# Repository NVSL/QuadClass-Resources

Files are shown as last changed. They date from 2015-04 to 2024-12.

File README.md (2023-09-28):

# The Quadcopter Class

Welcome to CSE176e Robotic System Design and Implementation (AKA, the Quadcopter Class).

This repo serves an the homepage for the course labs. It contains all
the lab write ups and several resources you will use throughout the
course.

- `labs` has all the labs. The write ups reference the starter repos they use.
- `Fusion 360` has the pre-built parts library, CAM files, and design rule files to use with Fusion 360.
- `Lecture Slides` has slides that aren't part of any particular lab.

Please see the [course home page](https://sites.google.com/ucsd.edu/the-quadcopter-class/home) or the [class calendar](ohttps://docs.google.com/spreadsheets/d/1cgSJm-5A6JrrA-iNKX8d2A0SE1PBk1CwzLvdhLKHuWY/) for schedule, due dates, and other logistical issues.

## A Note About Software Tool Names

The PCB design software we use is called Fusion 360. It used to be known as "Eagle". I've mostly updated the course materials to reflect this change.  If you see "Eagle" you should think "Fusion 360".

## Overview

We are going to build remote-controlled quadcopters from scratch in 10 weeks.

The goals for the course are for you to learn how to design, assemble, and program a moderately complex electronic device. The device you will build is a small, remote-controlled quadcopter similar to this:

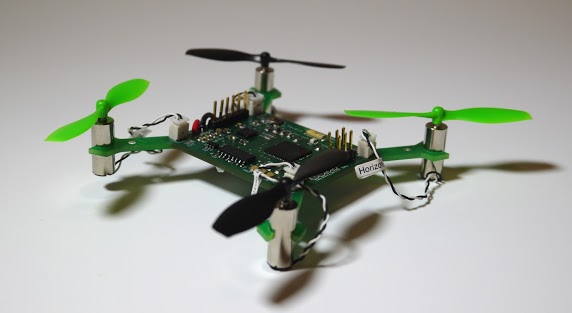
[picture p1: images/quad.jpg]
Example Quadcopter


In particular, you'll learn and/or practice these skills/topics:

- Printed circuit board design
  - Implementing a spec
  - Leveraging reference designs
  - Interpreting data sheets
  - Selecting parts
- PCB Assembly
  - Concepts
  - Moderately advanced soldering
- Embedded Systems Programming
  - Real-time
  - Resource constrained
- Basic Sensor fusion
- Basic Control Theory

## Labs

There are 10 labs divided into four sections. Deadlines are on the course homepage.

The slides for each lab are in the directory with the lab description.

### PCB Design

1. [Introduction To Fusion 360](https://github.com/NVSL/QuadClass-Resources/tree/master/labs/Introduction-To-Eagle)
2. [Building Parts In Fusion 360](https://github.com/NVSL/QuadClass-Resources/tree/master/labs/Building-Parts-In-Eagle)
3. [Building The Quadcopter Schematic](https://github.com/NVSL/QuadClass-Resources/tree/master/labs/Building-The-Quadcopter-Schematic)
4. [Laying Out The Board](https://github.com/NVSL/QuadClass-Resources/tree/master/labs/Laying-Out-The-Board)
5. [Manufacturing The Board](https://github.com/NVSL/QuadClass-Resources/tree/master/labs/Manufacturing-The-Board)

### PCB Assembly

6. [Assembling A PCB](https://github.com/NVSL/QuadClass-Resources/tree/master/labs/Assembling-A-PCB)

### Software

7. [Programming The Hardware](https://github.com/NVSL/QuadClass-Resources/tree/master/labs/Programming-The-Hardware)
8. [Sensing and Control](https://github.com/NVSL/QuadClass-Resources/tree/master/labs/Sensing-And-Control)
<!-- 8. [Sensing and Filtering](https://github.com/NVSL/QuadClass-Resources/tree/master/labs/Sensing-And-Filtering)-->
<!-- 9. [Implementing PID](https://github.com/NVSL/QuadClass-Resources/tree/master/labs/Implementing-PID)-->

### Flight

9. [Flight](https://github.com/NVSL/QuadClass-Resources/tree/master/labs/Flight)
10. [Cleanup](https://github.com/NVSL/QuadClass-Resources/tree/master/labs/Cleanup)

## Lab Equipment

The course requires several pieces of equipment:

1. A remote control.
2. A PID test stand.
3. A quadcopter prototype.
4. Miscelleneous cables, parts, etc.

You will also build a quadcopter, which you can also keep.

### Keeping the Remote

You cannot keep the remote you used in class. However, I a limited number of older remote boards that you can have if you really want one. Please talk to me near the end of the course, if you are interested.

### Returning the Equipment

The PID test stand, flight control board, remote, and other miscelleneous equipment you borrow for the labs must be returned or replaced (modulo normal wear and tear) before I will assign you a grade in the course.

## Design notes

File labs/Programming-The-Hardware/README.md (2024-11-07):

# Arduino, Wireless, and Quadcopter Hardware

This is big lab, but there shouldn’t be many surprises. You’re mostly getting parts and pieces together for future labs, but you do have to integrate everything into one app at the end, and integration is always harder than you think.  
There’s a lot to do. Get started!

## Pick your Team

You will work on this lab and all future labs in teams of two. You will need to create a team on Eaglint and via the github classroom interface. The name of your team in github classroom must match the team name you use in Eaglint, or Eaglint will refuse to check your work.

## Skills to Learn

1. Installing the Arduino GUI.
2. Programming your remote and the flight control board.
3. Communicating with the boards using an FTDI serial port.
4. Communicate wirelessly between the remote and the FCB.
5. Reading values from the controller gimbals.
6. Use the other features of the remote.
7. Driving a DC motor with PWM.

## Equipment, Supplies, and Software You Will Need

1. Create a team in eaglint. You _must_ do this before clicking the starter link below.
2. The starter repo for this lab: https://classroom.github.com/a/a_OCsamt.
4. Test stand and remote control part kit.
5. Laser-cut parts for a test stand and airframe.
6. 1 micro USB cable.
7. 1 flight control board (FCB).
8. Three LiPo batteries.
9. 1 set of motors.
10. 1 set of matched propellers (2xCW, 2xCCW)

### Your Remote Control

You are responsible for the care of the remote:

1. If you break it, you'll need to pay replace the broken parts.
2. Be reasonably gentle with the gimbals (joysticks). They are of high quality, but are not indestructible.

Unfortunately, you cannot keep the remote. However, it is pretty easy to build you own. Ask the professor, if you are interested.

### Your Flight Control Board and Test Stand

The flight control board (FCB) is a PCB very similar to the quadcopter
you will eventually build. It mounts to the test stand and will
provide a platform for your initial quadcopter firmware development.
The FCBs are provided for your use during the class.

## Preliminaries

### Install Arduino

Install Arduino 2.3.3. This is the only version we will be supporting in class.  
[Arduino Download](https://www.arduino.cc/en/software)

### Setup Your Firmware Development Environment

The repo you create and use for this lab will be the repository you use for your software development during the rest of the class. The `firmware` directory is organized as an Arduino Sketchbook, which means the Arduino toolchain and IDE know where to look for things. To use it, you’ll need to set that directory as your sketch book directory in Arduino.  
(`File->Preferences->Sketchbook location`).  
Then, enter your github repo firmware folder path, example: `../<github_repo>/firmware`

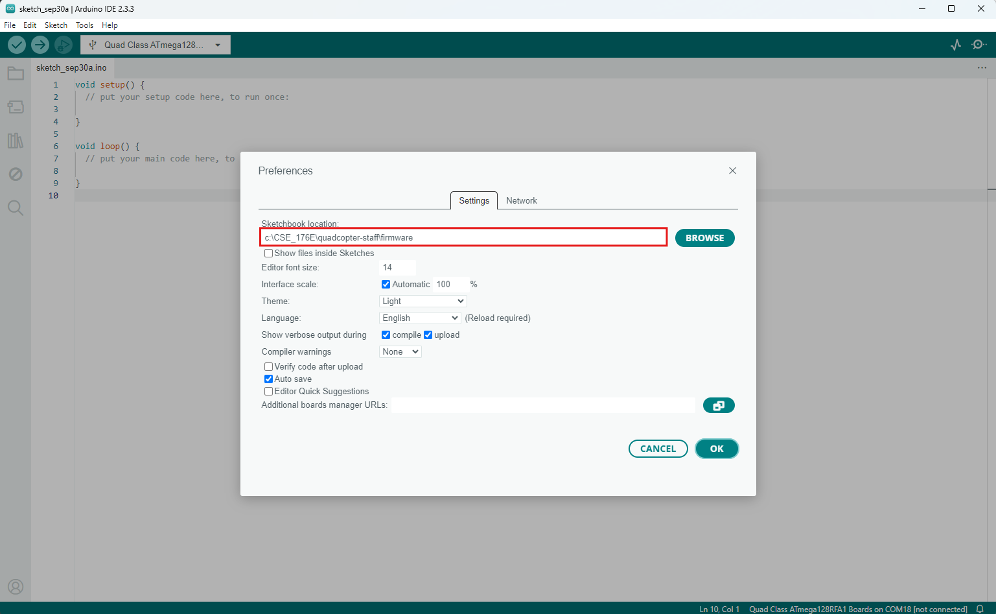
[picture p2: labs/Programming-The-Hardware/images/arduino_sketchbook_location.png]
Sketchbook Path


#### Add Board Definition Files

This will let Arduino talk to all the [Atmega128RFA](https://www.digikey.com/en/products/detail/microchip-technology/ATMEGA128RFA1-ZU/2208800) boards we will be using in this class, including your quadcopter.

- Clone the Arduino addon (https://github.com/NVSL/QuadClass_Atmega128RFA_Arduino_Addon) into `firmware/hardware`. You should end up with this directory `firmware/hardware/QuadClass_Atmega128RFA_Arduino_Addon/avr`.
- Restart Arduino. Then, under `Tool->Board` you should see `Quad Class ATmega128RFA1 Boards`. Select that board.
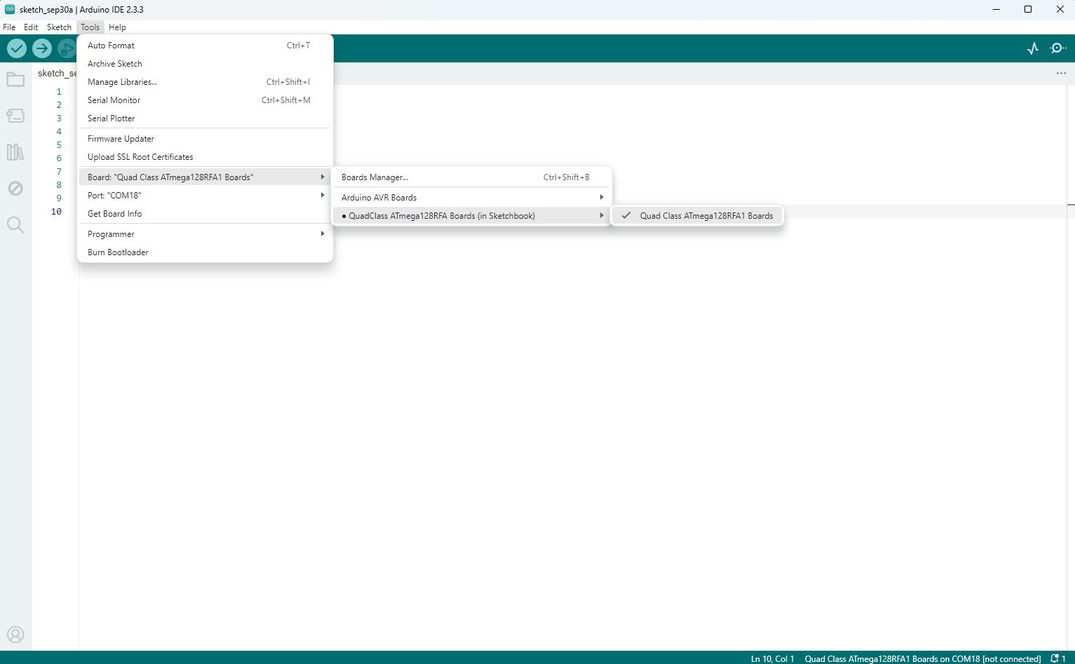
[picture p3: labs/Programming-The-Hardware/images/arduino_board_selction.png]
Board Selection
  
- Select `Tools->Programmer->USBTinyISP`

#### Install the Libraries

You’ll need a few libraries, so you might as well install them now, but you won’t use all of them in this lab:

Clone them into `firmware/libraries`.

1. Attitude, Heading, and Reference System (AHRS): https://github.com/NVSL/QuadClass_AHRS.git
2. LSM6DSOX library: https://github.com/NVSL/QuadClass-LSM6DSOX.git
3. Adafruit unified sensor library: https://github.com/NVSL/QuadClass_Sensor.git
4. Sparkfun SerLCD library: https://github.com/sparkfun/SparkFun_SerLCD_Arduino_Library.git

Here's the command sequence on my machine:

```
(cd ./firmware/libraries/; git clone git@github.com:NVSL/QuadClass-AHRS.git)
(cd ./firmware/libraries/; git clone git@github.com:NVSL/QuadClass-LSM6DSOX.git)
(cd ./firmware/libraries/; git clone git@github.com:NVSL/QuadClass-Sensor.git)
(cd ./firmware/libraries/; git clone git@github.com:sparkfun/SparkFun_SerLCD_Arduino_Library.git)
(cd ./firmware/hardware/;  git clone git@github.com:NVSL/QuadClass-Atmega128RFA-Arduino-Addon.git)
```

Go to Library Manager and install "Adafruit LSM6DS". A pop-up window will show up, click "Install ALL".  
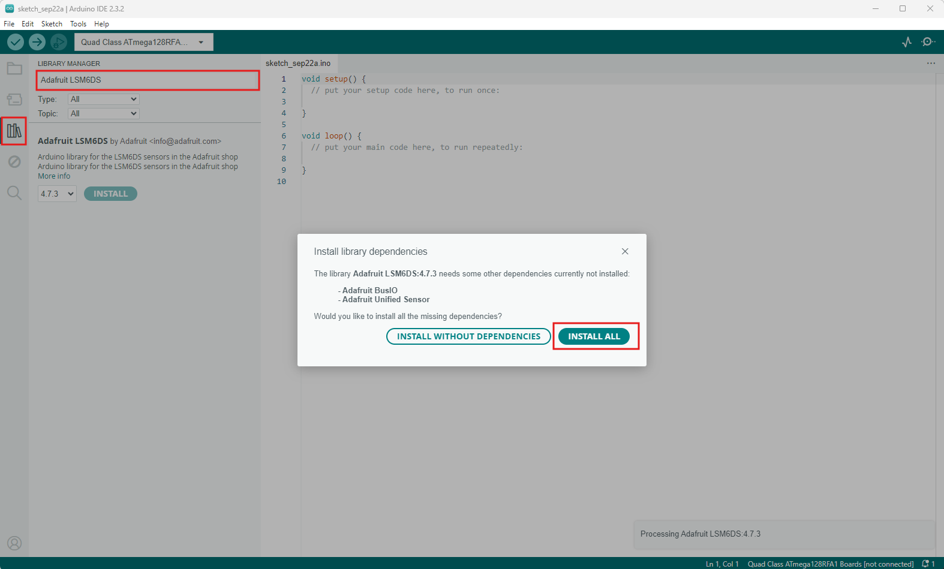
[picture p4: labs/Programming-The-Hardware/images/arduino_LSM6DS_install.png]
Install Adafruit LSM6DS


When you're done, the top few levels of your repo should look like this:

```
./firmware
./firmware/hardware
./firmware/hardware/QuadClass-Atmega128RFA-Arduino-Addon
./firmware/RFEcho
./firmware/RFEcho/RFEcho.ino
./firmware/RFChat
./firmware/RFChat/RFChat.ino
./firmware/libraries
./firmware/libraries/Radio
./firmware/libraries/SparkFun_SerLCD_Arduino_Library
./firmware/libraries/RotaryEncoder
./firmware/libraries/QuadClass-Sensor
./firmware/libraries/QuadClass-AHRS
./firmware/libraries/QuadClass-LSM6DSOX
./firmware/libraries/Adafruit_BusIO
./firmware/libraries/Adafruit_LSM6DS
./firmware/libraries/Adafruit_Unified_Sensor
./firmware/libraries/Remote
./firmware/libraries/SoftwareSerial2
./firmware/RFCount
./firmware/RFCount/RFCount.ino
./hardware
```

Restart Arduino and the bottom of your `Sketch->Include Library` menu should look something like this:

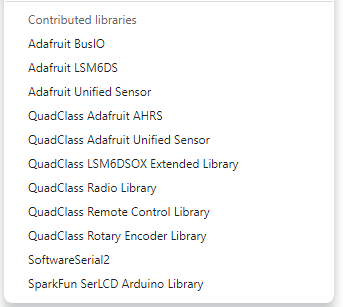
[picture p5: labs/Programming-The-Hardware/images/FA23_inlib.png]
Libraries installed


#### Getting Updates For the Starter Repo

Occasionally, I find bugs in the starter repo and push updates to it. To get them you need to 'fetch from upstream' using git. The first time you do this you need to do:

`git remote add upstream git@github.com:UCSD-Quadcopter-Class/QuadClass-Quadcopter-Starter-sp23.git`

Then, each time I push a new update you should do this:

```
git fetch upstream
git merge remotes/upstream/master
git push
```

I'll announce pushes on Piazza.

#### Create Your Firmware Source Files

Create sketches for your quad and remote control firmware.

- `firmware/quad_firmware/quad_firmware.ino` will hold the firmware (i.e., flight control software) for your quadcopter
- `firmware/remote_firmware/remote_firmware.ino` will hold the code for your remote control.

Add the following code to `remote_firmware.ino`:

```
#include <radio.h>
#include "quad_remote.h"      // Header file with pin definitions and setup
#include <serLCD.h>
serLCD lcd;

void setup() {
}

void loop() {
}
```

### Arduino Troubleshooting

Programming Arduino microcontrollers (i.e., transfering the compiled to the device) can be a temperamental process. If you get an error while programming the board, there are many different things you can try to make it work (some of which seem like magic):

- Make sure you have the right board and programmer selected.
  - On a Mac, this will be something like `/dev/cu.usbserial-AG0JL8H4`. It is definitely not anything like `tty.usbserial-AG0JL8H4` or `cu.Bluetooth-Incoming-Port` or `cu.iPhone-WirelessiAPv2`.
  - On a PC, it is probably the highest-numbered "COM" port.
- Try a different USB port. Laptops generally have multiple, internal USB hubs and some don’t play well with Arduino.
- Try a USB 2.0 port. Sometimes programming doesn’t work over USB 3.0. If your computer has a USB 2.0 hub use it. If not, get a USB 2.0 hub and plug the Arduino into that. On some machines the blue USB ports are 3.0 and black ones are 2.0.
- Unplug everything, quit Arduino, plug everything back in, restart Arduino.
- Google the error. Chances are you are not alone.

In rare cases, you may need to install drivers for the FTDI programming board. Read the How to Install FTDI Drivers Tutorial https://learn.sparkfun.com/tutorials/how-to-install-ftdi-drivers.

## Bringing Up the Remote

Your first task to "bring up" your remote. This means verifying that all of it's components work and that you can successfully access them via software.

**Note:** You don't need to assemble it anymore, we will provide an assembled remotes.
### Assembling the Remote

Many of you will receive a partially assembled remote. Follow along in here to add the parts that are missing.

**The pictures below are for an older model of the remote. The steps are very similar. Differences are noted.**

To assemble the remote you will need the following **FIXME CHECK**:

- 8x 1-inch standoffs
- 4x 1/2-inch standoffs
- 4x 3/8-inch standoffs
- 8x 1-1/2-inch screws
- 4x 1-1/4-inch screws
- 12x nuts
- 4x small zip ties
- 1x PCB
- 1x LCD
- 1x battery cable
- 2x gimbals
- 1x USB Micro cable

##### Steps

**All the Parts**

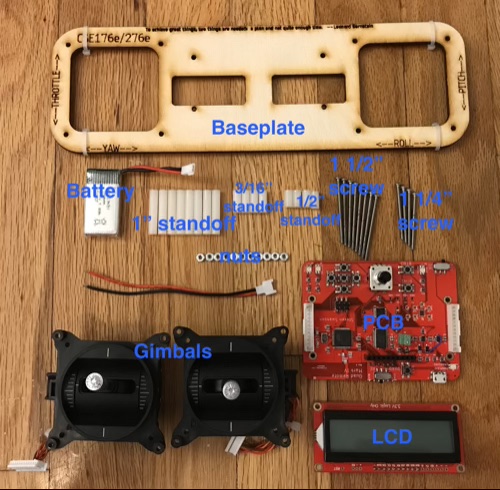
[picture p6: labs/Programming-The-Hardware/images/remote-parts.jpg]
Remote Parts


**Add Screws**

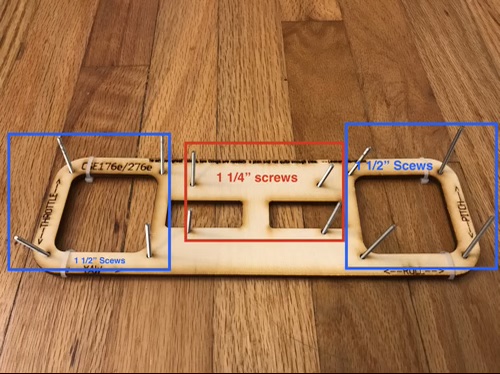
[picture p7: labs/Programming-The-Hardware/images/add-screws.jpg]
Add Screws


**Add Standoffs**

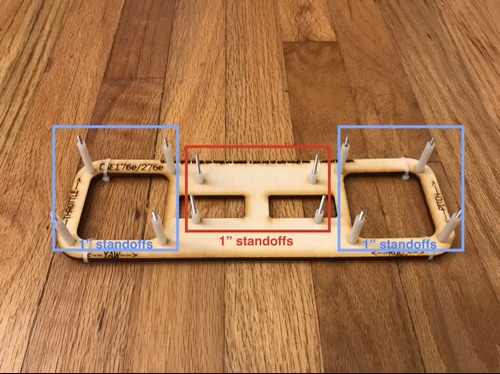
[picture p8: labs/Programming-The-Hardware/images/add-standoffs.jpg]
Add standoffs


**Add Gimbals and PCB**

The vertical axis of the left gimbal should not return to the center position automatically. The other gimbal axes will.

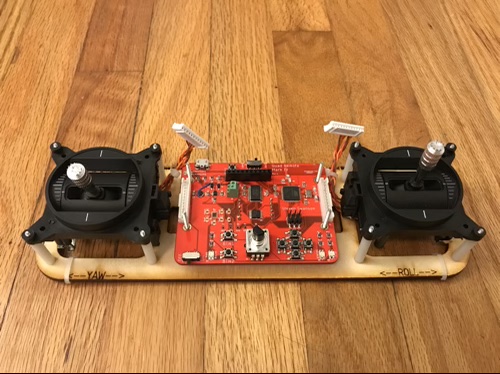
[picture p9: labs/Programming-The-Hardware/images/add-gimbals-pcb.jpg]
Add gimbals


**Screw in the Gimbals**

THe pictures shows nuts on the screws attaching the gimbals, but we don't use those any more. Instead, the screws should thread directly into the black plastic of gimbal. If they don't go easily, come see the TA or teacher, we may need to add threads to holes. Also, do not over-tighten the screws -- the plastic is quite soft.

**Plug in Gimbals**

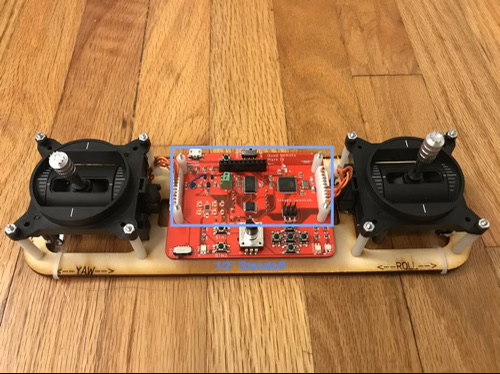
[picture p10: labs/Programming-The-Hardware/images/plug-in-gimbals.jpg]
Plug in gimbals


**Install Standoffs, LCD Nuts, and LCD**

The pictures show the nuts going _over_ the LCD, but they should actually go under. This makes it much easier to remove the LCD if you needed.

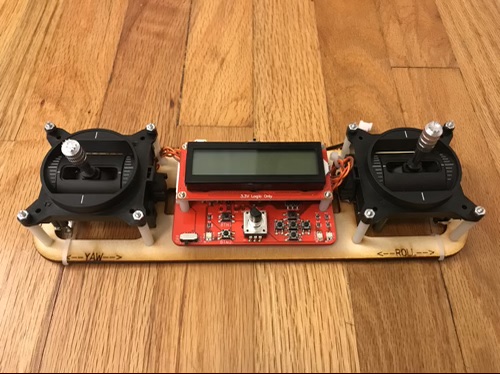
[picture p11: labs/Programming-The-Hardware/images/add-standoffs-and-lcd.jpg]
Install standoffs and lcds


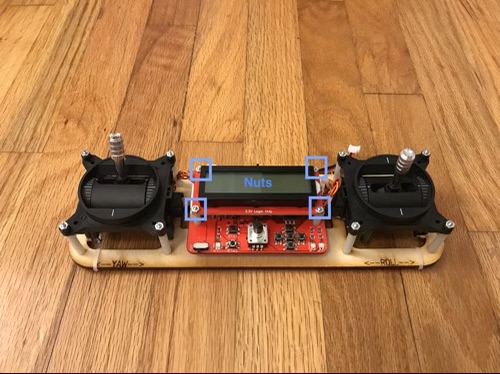
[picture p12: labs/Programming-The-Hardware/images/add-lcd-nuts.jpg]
Add LCD nuts


**Attach Zip ties as 'feet'**

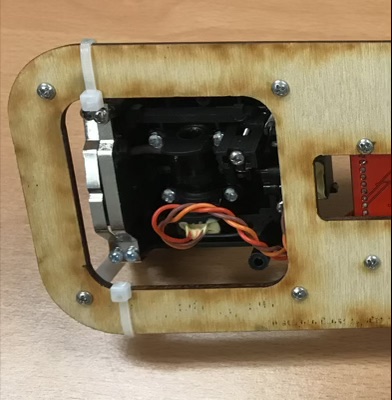
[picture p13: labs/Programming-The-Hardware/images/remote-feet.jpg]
Remote FTDI


### Installing a Battery

The remote can be powered either via USB or via a LiPo battery. It also has a builtin LiPo charger that will charge the battery when it's attached to USB. You'll have three batteries. Keep one charging on the remote and the other hooked to the FCB.

There two typese of connectors for the battery: white and green.

For the white connector, you can plug the battery directly into the connector.

For the green connector, you'll need connecta a "pig tail" to the green terminal block on the PCB.

Once that's done, you can plug the battery in by inserting the plug into the white connector.

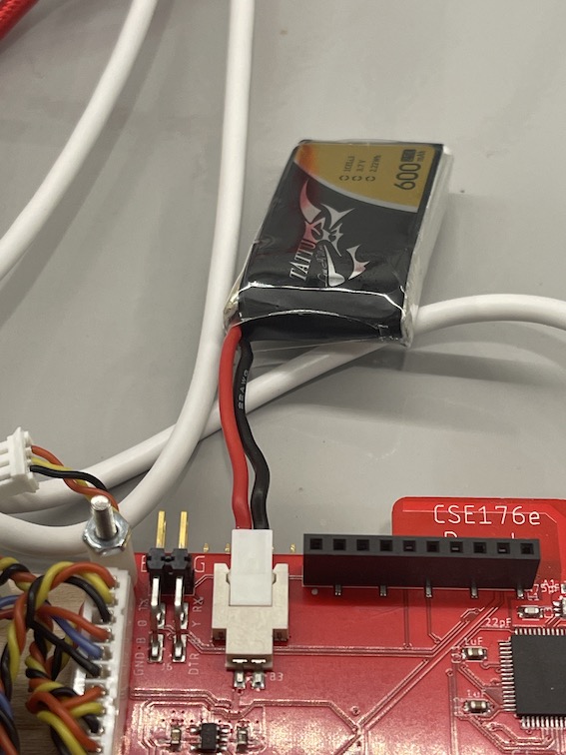
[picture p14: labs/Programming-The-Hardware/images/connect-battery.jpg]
Connect Battery


The wooden base of the remote has cutout to accomodate a battery. Apply a piece of _fuzzy_ velcro to the to the PCB under that gap (if there's not one already)

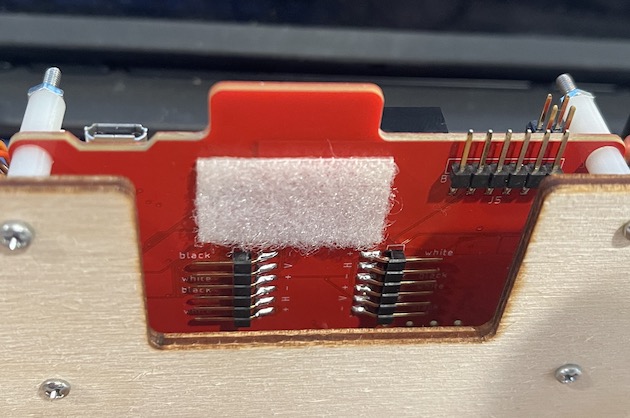
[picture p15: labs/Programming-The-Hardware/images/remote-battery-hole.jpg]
Remote battery hold


and attach the battery:

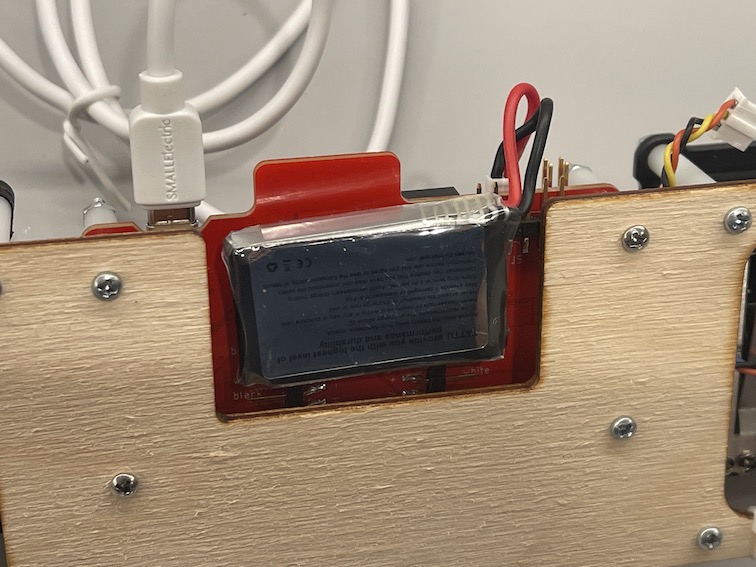
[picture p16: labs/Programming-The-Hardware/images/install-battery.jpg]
Install Battery


You may need to put velcro on the battery as well. If so, make sure to use the rough velco and make sure the velcro is oriented like this (note the position of the wire coming off the upper-right corner):

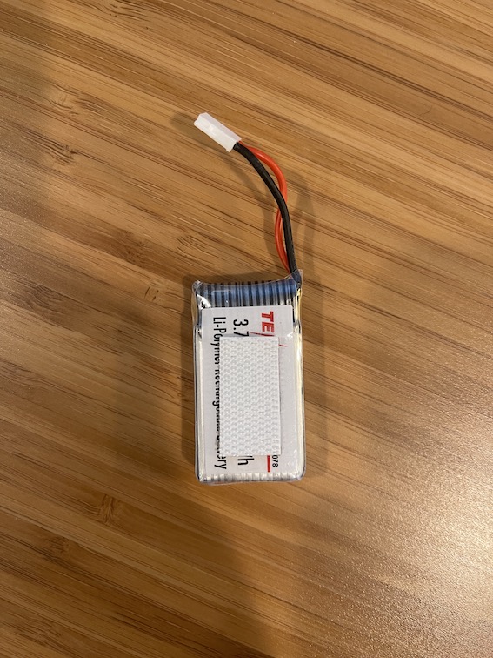
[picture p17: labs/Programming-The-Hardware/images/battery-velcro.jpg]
Battery Velcro


### Run a Test Program On the Remote

The Remote has a builtin USB-to-serial converter that allows it to program the microcontroller on the remote. It can also program the FCB via a cable. Whether it will program the remote or the quadcopter target is controlled by the `quad/RC` switch at the top of the remote.

Plug your USB cable into your laptop and the remote, and make sure you're Board, Port, and Programmer are set correctly:

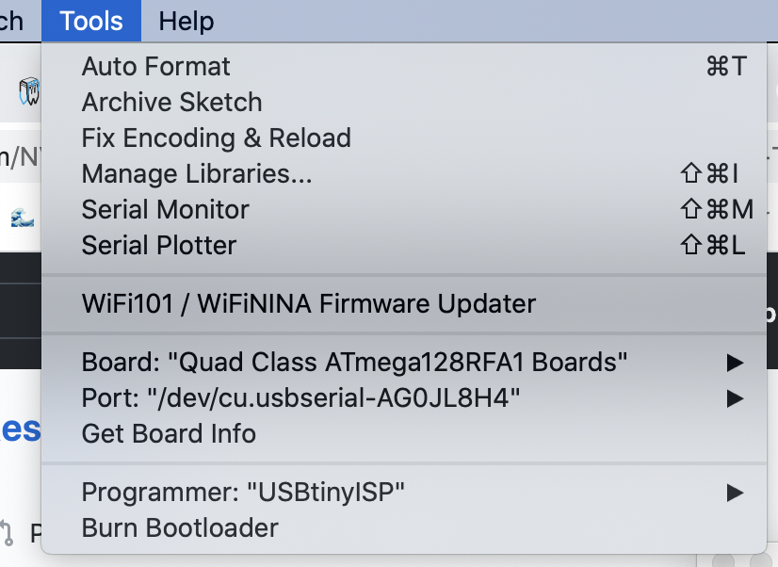
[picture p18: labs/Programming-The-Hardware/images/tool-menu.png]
Tool menu settings


Then...

- Set the "RC/Quad switch" located on the Remote Control board to 'RC'

- Open up `File->Examples->01.Basics->Blink`.

- Compile and download to the remote.

- One of the LEDs on the board will start blinking slowly.

- Open up `File->Examples->01.Basics->AnalogReadSerial`, and run it.

- Then, open `Tools->Serial Monitor`. You should find it printing a number at you. Moving the left stick on your remote should cause it to change.

- For fun, close the serial monitor, then `Tools->Serial Plotter` and you should be able to draw curvy lives by moving the left joystick.

### Reading the Buttons

The `QuadClass Remote Library` library provides access to the basic hardware features of the remote. You get access to the library with `#include "quad_remote.h"` and calling `quad_remote_setup()` in your Arduino `setup()` function.

The library provides a call-back-based mechanism for detecting when the user presses the buttons. Function pointers (e.g, `btn1_cb`) hold functions that will be called when a button (e.g., button 1) is pressed or released. The callbacks you set need to run quickly (e.g., ideally, they should not print anything to the serial port).

To see how it works open `Open->Examples->QuadClass Remote Control Library->knob_and_buttons.ino`. Run it,
open the serial monitor, push some buttons, and see what happens.

There is also a simple 'is_pressed()' function that you can use to tell if a given button is currently pressed. You should pass the `*_PIN` constant for the button you want to test. The `*_PIN` macros are in `quad-remote.h`.

Read the code to understand how it works.

### Reading the Knob

There's a similar mechanism for the knob. The library defines an object called `knob1`, and calls a callback (`knobs_update_cb`) when it's value might have changed (i.e., sometimes it'll be called even though the value remains the same). This funtion needs to run very quickly (e.g., it should not write anything to the serial port), otherwise you might miss some movement of the knob.

You can access the current value of the knob with `knob1.getCurrentPos()`. The knob can turn indefinitely in either direction and the number will grow and shrink accordingly. You can also set the current knob value with `knob1->setCurrentPos()` (see `knob_pressed()` in the example).

Look at `Open->Examples->Remote->knob_and_buttons.ino` and the `libraries/RotaryEncoder/RotaryEncoder.h` for details (Don't bother with `RotaryEncoder` example. It's broken and `knob_and_buttons.ino` is more useful). Run the example and turn the knob. The knob has a builtin button, too. It works just like the other buttons.

### Writing to the LCD

The remote has a fancy LCD screen with an RGB LED backlight (it's this: https://www.sparkfun.com/products/16397).

The `Remote` library sets up the lcd for you as an object called `lcd`.

The `knobs_and_buttons.ino` example shows how to use it: It displays the value of the knob and lets you move it's location around on the display. It's pretty faint because it's redrawing so quickly but it should be visible.

Here are the basic commands.

- `lcd.clear()` clears the display
- `lcd.home()` move the cursor to the top left position.
- `lcd.print(char *)` write some text to the display. It works with `int`, `float`, `char *`, etc.
- `lcd.setCursor(int c, int r)` Move the cursor to the `c` position of row `r`.

There's some other fancy stuff you can do, too, like scrolling, changing the contrast setting, and changing the backlight color. Checkout the examples, but note that the examples all assume I2C connectivity, but the remote uses `SoftwareSerial`, so you'll have to adapt/copy from the examples rather than running them directly.

### Reading the Gimbals

1. Write a function that reads values from the gimbals and use it to writes them to the serial port.
   - Check out [analogRead()](https://www.arduino.cc/reference/en/language/functions/analog-io/analogread/).
   - The [Arduino Serial monitor](https://www.arduino.cc/reference/en/language/functions/communication/serial/) will tell you how to get output to the serial port.
   - The function should go in your `firmware/remote_firmware/remote_firmware.ino`, which will slowly grow into your remote’s firmware.
2. Does the value you read from the gimbals vary across the gimbals’ full range of motion? If not, let us know.
3. Have your code scale the values you get from the gimbals so the full range of motion corresponds to the range 0-255. Arduino's `map()` and `constrain()` functions are useful here.

### Reading the Battery Voltage

Write a small function that uses `analogRead(BAT_SENSE_PIN)` to read the battery voltage, where `BAT_SENSE_PIN = A7`. Inside that function also print the battery voltage using `Serial.print()`.

In the setup function set the voltage reference as INTERNAL, `analogReference(INTERNAL);`, and the pin mode of `BAT_SENSE_PIN` as input. Remember also to properly configure the Serial.

Call the function inside the main loop with a reasonable delay. Check that the integer number (battery voltage) drops over time.

## Assemble your Test Stand

Parts:

- 1x FCB
- 1x Air frame
- 8x small wooden spacers
- 4x 1/2-inch (or 5/8th) screws
- 4x nuts
- 1 set of motors
- 4x small white zip ties
- 2x skewer
- 1x battery
- 2x test stand sides
- 1x test stand cross-brace
- 1x 4-pin programming cable
- 2x Clockwise Blades
- 2x Counter-clockwise Blades
- 4x blade guards

### Assemble the Frame

The test stand assembles without any tools, and should look like this when it's done:

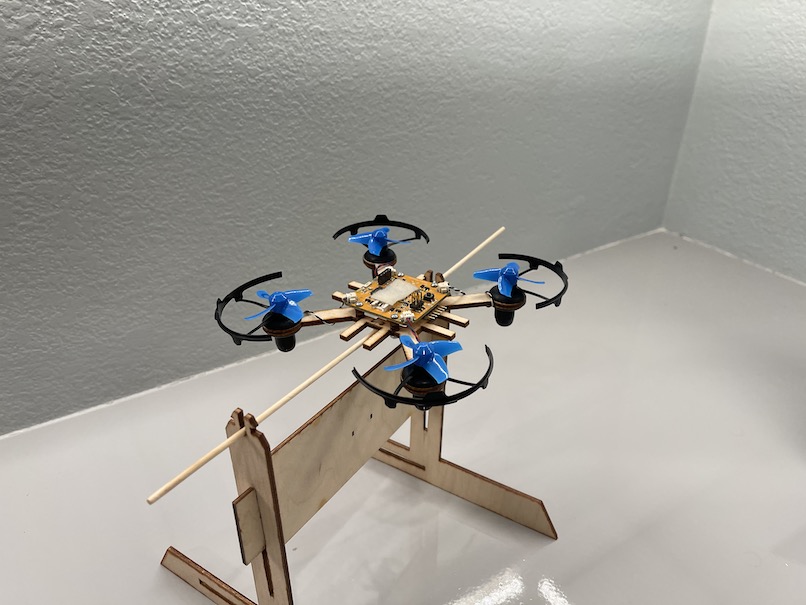
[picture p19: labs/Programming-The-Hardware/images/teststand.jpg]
Test Stand


1. The middle brace slides into the slots on the two end pieces. You can use either the vertical or horizontal slot.
2. The wooden dowel goes through the holes
3. You can attach two small zip ties to the down to keep it from sliding too much.

It's easy to disassemble as well, although the corners are a bit sharp.

**Note:** You don't need to assemble the FCB anymore, we will provide an assembled FCB.

### Assemble the FCB and Airframe

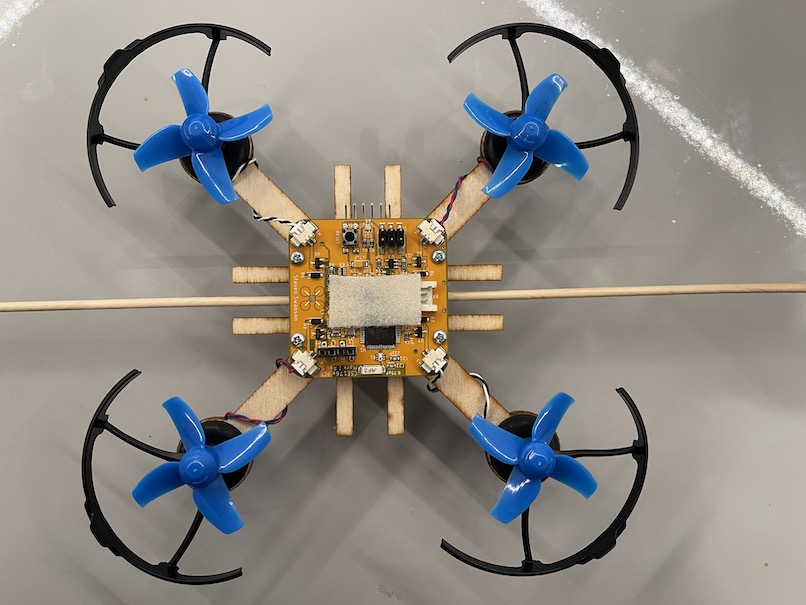
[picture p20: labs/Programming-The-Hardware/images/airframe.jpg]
Air frame


The FCB mounts to the wooden air frame as shown above by following the steps below:

1. Use four screws and nuts to attach the FCB to the airframe. Use 2 of the wood spacers on each screw to provide a gap between the two. The photo shows a single space, but you will need 2.

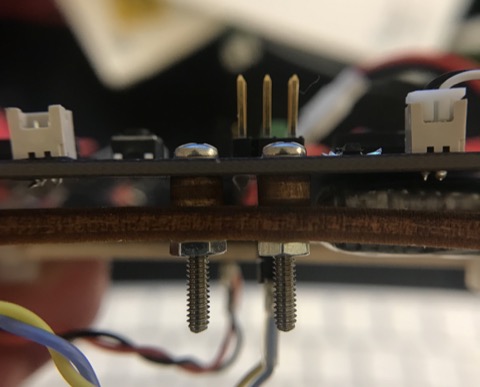
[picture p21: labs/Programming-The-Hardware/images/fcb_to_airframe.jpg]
Air frame


2. Use another four zip ties to attach two of your dowels to the air frame to the dowel. One dowel should go above the air frame the other goes below. They should be snug but not super tight. They need to hold it securely. You should be able to move the dowel back and forth with some friction.

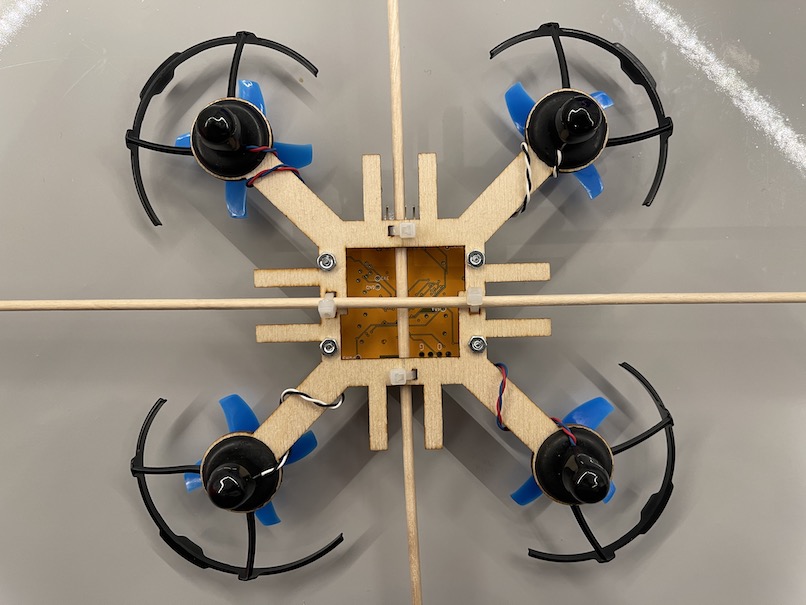
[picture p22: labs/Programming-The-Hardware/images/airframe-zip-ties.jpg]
Air frame


3. Trim the tails of your zip ties as short as you can. Nail clippers work well.

4. Put a piece of _fuzzy_ velcro on the top of the FCB as seen above.

5. Plug a battery into the connector on the top of the board. If the battery doesn't have velcro, add _scratchy_ velcro to the battery as described for the remote. Mount the battery on FCB.

6. The motors plug into the four recepticals on the FCB. You need two read/blue and two black/white motors and matching colors need to diagonally opposite eachother (like in the picture above). It's hard to see but there is "RB" on the corner next to the connectors for the red/blue wires and "BW" next to the connectors for the black/white wires.

7. Insert 4 rubber grommets into the holes at the end of each arm. Work carefully so you don't break your airframe. It takes some effort.

8. Wrap the wire around the arms once or twice and then insert the motor through the grommet. It is a tight fit.

9. Install the four propellers. You need two clockwise and two counter-clockwise motors. The clockwise props go on the red/blue-wired motors. The counter-clockwise props go on the black/white-wired motors. See note below about identifying clockwise vs counter-clockwise props.

10. Install the four motor covers on the bottoms of the motors. This will give the quadcopter 4 rubber "feet".

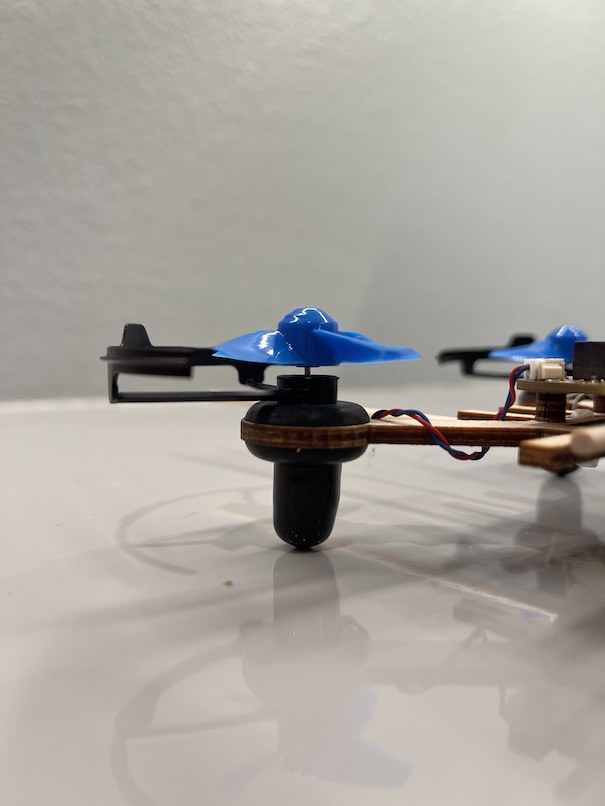
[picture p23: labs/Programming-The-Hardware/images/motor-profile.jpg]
install motors profile

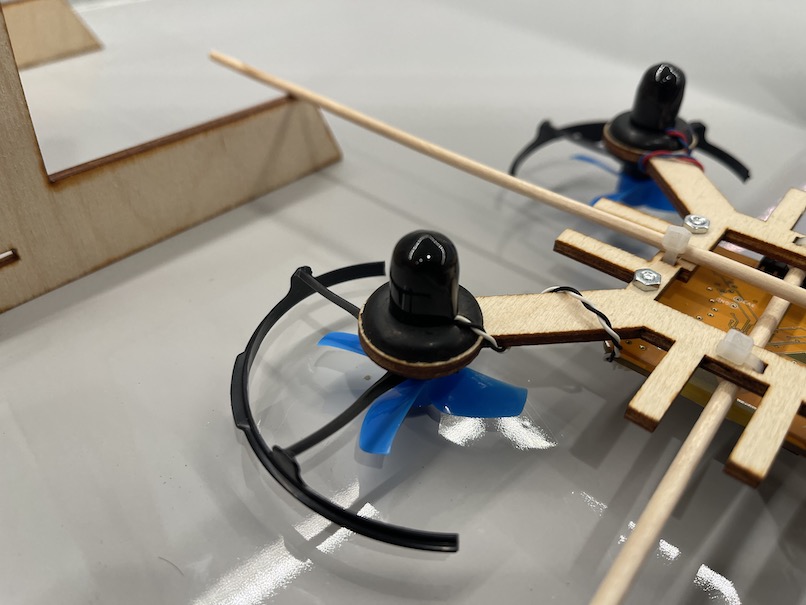
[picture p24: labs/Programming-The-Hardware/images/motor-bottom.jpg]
install motors upside down


#### Identifying Props

We have two different styles of props. The first have two long, slender blades. The clockwise props are labeled labeled "A" (see below) and the counter-clockwise props are labeled 'B'.

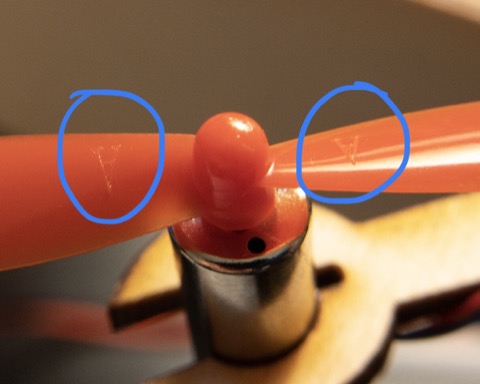
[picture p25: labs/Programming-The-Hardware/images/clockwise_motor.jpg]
thin clockwise

this counter-clockwise

The second type of prop are smaller and have four wider blades. They have arrows on them showing the direction they spin.

thin clockwise
this counter-clockwise

#### Removing Props

Getting the props off can be hard. You have a little lever tool in your kit to help with this:

prop remover

## Bringing up the FCB

The FCB has three key hardware components you'll need to test: The microcontroller, the accelerometer, and the motors.

**Note:**  Do _not_ call `quad_remote_setup()` in your quadcopter firmware.  It will mess everything up.

### Turning on the FCB

To turn the FCB on you need to first connect the battery to the FCB and the then move the switch in the FCB from OFF to ON.

### Flashing the Bootloader

Flashing the bootloader is a step you typically performance once after a board is manufactured. It installs a small piece of software that makes the board compatible with Arduino.  You'll need to do this with your quadcopters when they are manufactured. We are doing it here for practice.

[Flashing the bootloader and bringing your board up](https://github.com/NVSL/QuadClass-Resources/blob/master/labs/Assembling-A-PCB/Flashing-The-Bootloader.md)

### Run a Test Program on the FCB

The FCB can be programmed via the remote control's USB-to-serial converter. The colorful 4-strand cable is for this purpose. The 2x2 female end connects to the remote. The 1x4 male end connects to the FCB. The pins on both boards are labeled by color ('G', 'B', 'O', 'Y'). It can connect to the FCB from either top or the bottom.

FCB FTDI

Remote FTDI

- Set the `RC/Quad` switch to "QUAD".
- Run the `Blink` example. The light should blink.
- Run the `AnalogReadSerial` example. It will print at you, but the number won't change.

### Reading from the IMU

Load, compile, and run `Open->Examples->QuadClass LSM9D6SOX Extended Library->quadclass_lsmd6sox` on the FCB. Open the serial monitor (You will probably need to adjust the BAUD rate to 115200 using the menu in the top right corner), and you should see something like this:

IMU Output

Shows the raw sensor readings from your IMU. As you move the FCB, they should respond accordingly. See if you can find gravity. It's 9.8 m/s^2.

### Driving the Motors

The motors on the FCB are attached to pins 8, 3, 4, and 5.

Add some code to `firmware/quad_firmware/quad_firmware.ino` to control the speed of the motors, and use the functions to run the motors at different speeds. [analog_write()](https://www.arduino.cc/reference/en/language/functions/analog-io/analogwrite/) will be useful.

To avoid injury take the following precautions

1.  Be careful of the propellers on the motors. They can hurt you.
2.  Before you start, make sure the airframe is in the “locked” position. This means mounting it on the test frame and sliding the stubby arms into the slots on the sides of the test stand, like this:

Docked FCB

#### If Your Motors Spin the Wrong Way

Some of the motors we purchased are wired backwards: The Red-Blue motors and the Black-White motors spin in the same direction. To fix this, you can use a pin to gently lift up the white tabs on the motor plug to remove the wires and the reinsert them. Here's a video showing how: https://youtu.be/G3APCQteYaQ.

## Using the Radio

**Note:** In your `setup()` function, you should call `rfBegin()` after you
call `quad_remote_setup()`, otherwise things won't work.

The microcontroller on the remote and the FCB (and eventually your
quadcopter) has a built-in radio. We will use it to send commands
from the remote to the FCB and to return telemetry.

First, find out your groups assigned channel. You'll need to edit the
examples below to pass a channel number to `rfBegin()`. Eaglint will
assign you a channel number. It's at the top of your list of group
design checks.

To test the wireless, open `firmware/RFCount/RFEcho.ino` and run it on
your FCB.

Then run `firmware/RFChat/RFChat.ino` on your remote. Open the serial
monitor, set the BAUD rate to 9600 (while it's connected to the remote) and type some text into the field at the top, and hit return.
It'll bounce the data off the FCB and print out the result. You might
get some garbage too, don't worry about it.

Look at the `RFChat` code to understand how it works: It checks if
data is available from the radio and writes it to the serial
port. Then, it reads data from the serial port and writes it to the
radio. Note that it sends and recevies multi-byte packets.

You'll notice that the radio library blinks one of the LEDs when data is sent or received.

## Sending Useful Data

Your next task is to think about how you will transmit data from your
remote to the quadcopter. A reasonable approach is to create a `struct`
that holds all the control values you want to send to the
teststand/quadcopter and transmit that struct, using `rfWrite()`. You
should include the gimbal values and the buttons.

There are some caveats:

First, you must tolerate the fact that the the radio channel you are using is a shared resource (it's the same RF range as WiFi). This means you may pick up data that is not yours, so you must be able to tell which packets are meant for you and which aren't.

One way to do this is to include a “magic number” in your command struct so
you can make sure you are getting commands from your remote and not
some other random data or packets from another team or noise. If you want to be more careful, you can include
a checksum as well. For instance, the last entry in the struct could
hold the `XOR` of all the other words in the struct. If they don’t
match, it’s a packet from somewhere else.

**Note:** If you receive a bad packet, you should called `rfFlush()` to make sure there's no unread data in the radio's buffers that will cause future calls to `rfRead()` to read misaligned data.

Second, don’t spam the world with your radio traffic. Modify your
remote firmware to send the command packet between 10 and 20 times per
second. The `millis()` functions (search for “arduino millis") will
help you here.

Third, your struct and the related function will be shared between
your quadcopter firmware and your remote firmware. The clever way to
do this is to create your own Arduino library that holds the struct
and related code. Otherwise, if you change it in one place, you’ll
have to remember to change it in another. This violates the [DRY
principle](https://en.wikipedia.org/wiki/Don%27t_repeat_yourself). Here's a tutorial on writing an Arduino library: https://www.arduino.cc/en/Hacking/libraryTutorial.  
Or you can look at the librarise in your repo for guidance (`firmware/libraries`).

To test it, program the test stand board to receive the data from your
remote and print it out. Verify that the values change as you move the
gimbals, etc.

### Reading the Battery Voltage on The FCB

Write a small function that uses `analogRead(BAT_SENSE_PIN)` to read the battery voltage, where `BAT_SENSE_PIN = A7`.

In the setup function set the voltage reference as `INTERNAL` with `analogReference(INTERNAL);`, and the pin mode of `BAT_SENSE_PIN` as `INPUT`.

The range of potential values returned from `analogRead()` is 0-1023.

The values you read from analogRead() are different based on battery level, so you'll have range of interger number that map the percentage of battery level. Also, remotes and quads have different value range.

You need to measure a value when the battery is empty, then measure a number when the battery is full, that's the range of the battery in interger number, than you need map that to percentage.

**Note:** The battery voltage level is not stable, sometime it will change in a wired curve, the value you measured is only the rough reference of the battery level. And there are also variance between different batteries.

### Blinking the LEDS

The FCB (Flight Controller Board) has eight LEDs. Four at the top (2 LEDs in each LED package), and four at the bottom.

The four LEDs at the top are addressed individually, and the software pin numbers are `LED1 = 16; LED2 = 17, LED3 = 18, LED4 = 36`. Write a function that turns on and off (blinks) these LEDs, choose any delay which makes the blinking visible (e.g., 1 second). Remember to set the pin mode of these LEDs as output.

The four LEDs at the bottom are addressed using a single pin which outputs PWM (Pulse Width Modulation). With PWM we can control the brightness of an LED. The software pin number is `PRETTY_LEDS = 34`. To write to this pin you need to use `analogWrite(PRETTY_LEDS, VALUE)`. Write a function that changes the brightness of the four LEDs using your preferred delay (e.g., 1 second). Remember to set the pin mode as output.

## Putting it All Together: Remote Controlled Motors and LEDs

Modify `firmware/quad_firmware/quad_firmware.ino` and
`firmware/remote_firmware/remote_firmware.ino` so you can arm your
FCB, calibrate your gimbals, and control your motors’ speed with the
remote.

### Calibrating Your Gimbals

The potentiometers in your gimbals are imperfect, so they need to be
calibrated. As you move them around, you'll notice that the values
don't go from 0 to 1023 (the full range of the microcontrollers ADC).
My yaw control, for intsance, only goes from 57 to 906. You'll need
the actual values for your gimbals so you can know, for instance,
where the neutral position for pitch, yaw, and roll are. To collect
these values, you'll need a calibration mode. The Arduino `map` functions is useful here.

A few things are required in your calibration mode:

1.  You don't have to do it every time your quadcopter restarts.

2.  You can't accidently enter it while your quadcopter is flying (since it requires you moving the sticks all over the place)

3.  The LCD should provide feedback about when calibration is in progress and when it's finished.

For #1, the Arduino EEPROM library is useful:
https://www.arduino.cc/en/Reference/EEPROM. It let's you store data
across resets.

For #2, you should only be able to enter calibration mode while the
quadcopter is not armed (see below). You will also need a way to
trigger calibration mode (e.g., pressing one of the buttons).

### Arming your FCB

The propellers are sharp enough and fast enough to hurt you. To
prevent accidents, your firmware should require you to "arm" your
quadcopter before it will turn on the motors.

Our arming sequence is to put the both gimbals in the lowest,
outermost position (left gimbal to lower-left, right gimbal to lower-right). This position is useful in two critical ways: 1)
the pilot is unlikely to do it by accident and 2) it ensures that the
throttle is at 0 when the quadcopter is initially armed.

Requirements:

1. Turn on the LED on the quadcopter when it is armed.
2. Provide feedback to the pilot (via the remote) that the quad is armed.
3. Make one of the remote buttons disarm the quad.
4. The quadcopter and remote must agree about when the quad is armed.

For #4: For instance, if your reset your
remote, the FCB should be disarmed. If you reset the FCB it should
disarm and remain disarmed until the remote arms it again. If you press the button to disarm, it should disarm the quad. If the remote turns off, the quad should disarm.

### Throttle Control

Once the FCB is armed, the throttle gimbal (the vertical axis of the left
stick) should control the speed of all four of your motors.

Make sure of the following:

1. When the stick is all the way down, the motor should turn off (I.e., writing 0 with `analogWrite()`).

2. When the stick is all the way up, you should be driving the motor at full power (i.e., writing 255 with `analogWrite()` )

3. As you move the stick, motor power should vary smoothly with the sticks position. (i.e., If the stick is at its midway paint, you should be writing 128).

4. If you push up on the stick when it is all the way up or down on the stick when it's all the way down, it shouldn’t behave strangely. Achieving this will require you to deal with non-idealness of the gimbals. The Arduino `constrain` function is useful here.

## Turn in Your Work

### Commit Your Code

1. Your remote firmware in `firmware/remote_firmware/remote_firmware.ino`.
2. Your quad firmware in `firmware/quad_firmware/quad_firmware.ino`.
3. Any other code you created (e.g., a library with your radio packet format).

### Demo Your Code

1. Demo your remote controlled motors.
2. Complete the reflection for this lab: https://docs.google.com/forms/d/e/1FAIpQLSfB8XsDV8FtTZYO1mv3FZrd9mUs1hDlFvQxnfAK0K2zptTjxQ/viewform

### Rubric

Possible points: 10

Check list (-1 point for each missing item):

1.  No motor activity when disarmed.
2.  Motor control active when armed.
3.  User feedback on the remote when the quad is armed.
4.  Arming turns on FCB LED.
5.  FCB reset disarms.
6.  Remote reset disarms.
7.  Calibration works.
8.  Calibration values saved.
9.  Calibration mode unavailable when armed.
10. Calibration feedback on LCD.
11. Pushing sticks past calibrated values doesn't result in strange behavior.
12. Zero motor activity at 0 throttle.
13. Throttle smoothly controls motor output across full gimbal range.
14. Turning off remote disarms quad.
15. Battery measurement on the remote.
16. Battery measurement on the FCB.

You will lose one point for each day late your solution is.

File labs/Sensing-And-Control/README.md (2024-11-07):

# Sensing and Control

To be completed in your groups.

Check the course schedule for due date(s).

## Skills to Learn

1.  Read data from the IMU.
2.  Using the Arduino plotting tool.
3.  Configure the builtin filters.
4.  Implement a complimentary filter in software.
5.  Tune the filters to provide good readings of FCB orientation.
6.  Implement a PID control loop in Arduino.
7.  Tune a PID control loop

## Equipment, Supplies, and Software You Will Need

1. Test stand
2. Remote control

## Tips

- This is a big lab, don't delay in starting.
- Your algorithms will have some parameters to tune. The remote's knob and buttons are meant to help tune them. You can use the knobs on your remote control to changes these dynamically, it will make tuning much faster than having to recompile.
- You can use the buttons too. For example, you could use the buttons to switch between parameters and adjust them with the knob.
- Some enterprising groups have also use the gimbals to set parameters too.
- You can send information over the serial port to your laptop to provide feedback to the user.
- If you stall the motors (i.e., hold them still with the throttle on), it may cause either your IMU reset, which will make it stop reporting any data.
- If your FCB resets when you turn on the motors, it's likely your battery is dying.
- Your IMU stops returning sensible numbers, it's likely your battery is dying.

## Part I: Sensing and Filtering

You cannot control what you cannot measure.

In this lab, you will use the IMU and some software to accurately measure the orientation of the quadcopter. In the next lab, you'll use this measurement as the input to a control algorithm that will keep the quadcopter stable.

### Reading Data from the IMU

Verify that your FCB is working properly and that you can program it and that you can read from the IMU by re-running your code from the previous lab.

The IMU provides a 3-axis accelerometer and a 3-axis gyroscope. You won't use the accelerometer data directly. Instead, your code will use them to compute the pitch and roll angles. You installed the library for this in the previous lab (https://github.com/NVSL/QuadClass_AHRS).

The key function in this library is: `Adafruit_Simple_AHRS::getQuadOrientation()` that fills in a new struct: `quad_data_t` with all the information you'll need: pitch and roll angles and the three axes of the gyro. There is also an example: `File->Examples->QuadClass AHRS->ahrs_quad_lsm6ds0.ino` that will print out these values.

I believe that you should not need to modify any of these libraries. If you find that you do, go ahead, but please let me know (or submit a pull request!).

### Plotting Data

Arduino has a nice data plotting facility built in. You print out numbers on a line, separated by spaces, it will plot each column of numbers in a different color in real time. Just select `Tools->Serial Plotter`. Any non-numeric data is ignored.

For best results, set your serial port bit rate to 115200. This the argument to `Serial.begin()` in your `setup()` function.

I have been having some trouble getting the serial port to work at 115200. For unclear reasons sometimes it will only work up to 19200. 9600 always works, but it's slow, so the graph is not very responsive.

Integrate the code from the example into your code for remote controlled motors from the last lab and have it plot the pitch euler angle (`.pitch` in the `quad_data_t` struct) and the pitch rate (`.pitch_rate`) from your IMU.

### Dealing with Noise

If you turn on the motors, you'll notice the output of the IMU gets noisy due to vibrations from the motorts. If you can't accurately sense the orientation of your quadcopter, you can't hope to control it.

To see the problem, use the sketch you just created. As you move the pivot platform with your fingers, you should see the curve swing back and forth pretty smoothly. Now try increasing the throttle to the motors using the remote control. You'll notice that curve becomes very jagged -- not smooth at all.

This is a big problems because it means that 1) the instantaneous measurements of your orientation are not accurate and 2) the derivative of your orientation is wildly unstable (since it bounces between positive and negative values). We need both the orientation and its derivative to be well-behave in order to stabilize the quadcopter (you'll see why in the next lab).

We will address this problem in two ways:

1. Applying filtering in software using a complementary filter.
2. Using the IMU's built in filters by configuring registers.

### Filtering in Software (Complementary filter)

You can filter out some of the noise in software by combining the readings from the accelerometer and the gyroscope. The AHRS library gives you Euler angles (i.e., degrees) for your quadcopter's orientation. These do not drift over time, but they are quite noisy when your motors are running.

The gyroscope gives you angular acceleration (i.e., the derivative of the Euler angles). The gyroscopes are less noisy than than the accelerometers. You could recover the Euler angles by integrating the gyroscope outputs, but the resulting measurement will drift over time due to accumulated error.

Our goal is to combine these two to use the accelerometer to avoid drift while using the gyroscope to avoid noise. The easiest way to do this is with a [complementary filter](http://www.pieter-jan.com/node/11). The math is simple and it's pretty intuitive.

The filter is weighted average of two terms:

1. The previously measured Euler angle + the integral of the gyroscope measurement since that measurement.
2. The current Euler angles measured from the IMU.

The filter's single parameter (called the _complementary gain_) ranges from 0 to 1 and controls how each of these terms contributes to the output. The higher the gain, the more influence the gyroscope has over the output.

Complementary filter (cf) equation:

```
cf_ange = (gain) * (cf_angle + (gyro_raw * RAD_TO_DEG * dt)) + (1-gain) * (acc_angle)
```

Where:

- `cf_angle` = Complementary filter angle
- `acc_angle` = Euler angles from `Adafruit_Simple_AHRS::getQuad()`
- `gyro_raw` = Gyroscope measurement from `Adafruit_Simple_AHRS::getQuad()`
- `gain` = Complementary gain
- `dt` = delta time

Notes:

- The `gyro_raw` value is in radians and needs to be converted to degrees.

```
#define RAD_TO_DEG 57.295779513082320876798154814105
```

- For dt (time), use the arduino funcion `millis()`. You want the time between loops, not the time now.

- Is advised to compare `acc_angle` to `gyro_angle` to check if both output a reasonable angle when tilting the FCB. The `gyro_angle` formula is the following:

```
gyro_angle = gyro_angle + gyro_raw * RAD_TO_DEG * dt
```

- When adjusting the gain from 0 to 1 you should see the complementary filter moving either to `acc_angle` or `gyro_angle`, depending on the gain value.
- You need to implement the complementary filter for both `pitch` and `roll`, we won't implement `yaw`.

I recommend watching this video to learn more about complementary filters: https://www.youtube.com/watch?v=6AoJ8wr8G6A

### Filtering using the IMU registers

The IMU has a bunch of settings that control how it collects and reports data. It also has some built in filters that can remove noise from its output. This is great, because it doesn't place any load on the microcontroller. Unfortunately, the documentation is kinda terrible.

Here's some basic terminology:

1. A low-pass filter allows the low-frequency component of a signal to pass through.
2. A high-pass filter allows the high-frequency component of a signal to pass through.

Generally, we would like the low-frequency information from the accelerometers and some part of the higher-frequency information from the gyroscopes.

#### Read Key Sections of the IMU Datasheet

- 6.4
- 9.12
- 9.13
- 9.17
- 9.18
- 9.19

#### Configure the Gyroscope and Accelerometer to Prevent Clipping (Sensitivity)

"Clipping" occurs when a measured value exceeds the range the IMU can handle. For the gyroscope, this means it rotates too quickly.
Clipping will show up as a flat plateau where a maximum should be on a graph of the gyro output. This is bad, because we will be relying on the integral of the gyro data to approximate Euler angles.

Use `lsm.setGyroRange()` to adjust range of values the gyros measure to eliminate the clipping. Use `lsm.setAccelRange()` to adjust the range of values for the accelerometer so it can measure at least 1G.

#### Adjust the Output Data Rate (ODR)

Adjust the output data rate (ODR) so it's higher than the rate at which you are sampling the data from the IMU. If the ODR is lower than your sampling rate, you'll read the same value repeatedly.

The AHRS example prints the latency for each trip through the loop at the beginning of each line (usually ~4ms). Your sampling rate is 1/latency (e.g., 250Hz). You can set the ODR for both the gyro and the accelerometer using `lsm.setAccelDataRate()` and `lsm.setAccelDataRate()`. See Table 44 and Table 48 for selecting the ODR.

#### Setup the Low-Pass Filter on the Accelerometer

The accelerometer can be configured as a low-pass filter or high-pass filter, this filter is called composite filter and can be setup using `lsm.setAccelCompositeFilter()`. The composite filter is shown in Figure 16 and 17, and the configuration register in Table 65.

We want the accelerometer to be configured as a low-pass filter to reduce noise, check how do this configuration using the function parameters.

You also need to set the cutoff for the low-pass filter of the composite filter, also referred as `LPF2`, by setting an ORD Ratio. The cutoff is set by dividing the ODR by the ODR ratio. For an ODR of 208 Hz and ODR/4, the low-pass cutoff is 52Hz.

#### Adjust for Offsets

When your FCB is still and level, it will probably not return zero pitch and zero pitch rate. When your FCB starts up (or maybe when you arm it) it should check the values coming from the IMU to see what offsets you are measuring. You should correct for these offsets so that the measured values are correct by subtracting the value measured at calibration, e.g. (`calibrated_angle = acc_angle - offset`). Do this for `acc_angle` and `gyro_raw`. Make the offsets variables global so that you can access them in all functions.

#### Coding Conventions

You can do all this tuning in a function similar to `setupSensor()` from the IMU example program. The example configures the IMU for all the values described above. Make sure you understand how it is working before you proceed.

In your code, you _must_ use the macros and constants defined in [QuadClass_LSM6DSOX.h](https://github.com/NVSL/QuadClass-LSM6DSOX/blob/main/QuadClass_LSM6DSOX.h) and [Adafruit_LSM6DS.h](https://github.com/adafruit/Adafruit_LSM6DS/blob/master/Adafruit_LSM6DS.h). If you show me code with magical hexadecimal values in it, I will tell you to go make your code readable first by using the macros and constants.

#### Target Values

You should configure the IMU's filters as follows:

1. You need to set the both gyroscope's and accelerometer's range to avoid clipping.
2. The ODR for both gyroscope and the accelerometer should be 208Hz.
3. You should configure the accelerometer's LPF2's cut off frequency to be 10.4Hz.
4. You should not use the HPF on the gyroscope.

### What Your Output Should Look Like

For the completion of this lab, your demo will be you wiggling the airframe on your test stand with your motors going full blast and the plotting curves moving responsively but smoothly in response.

The output of your complimentary filter will be an estimate of your current pitch angle. When you have your IMU filters set properly and your complimentary filter set correctly, you should observe the following:

1. No clipping.
2. With the motors off and the platform still, your estimated pitch angle should not change, even over long periods.
3. With the motors off and the platform moving, the maxima and minima for the pitch angle should align with the zeros of the raw gyro measurement. The pitch angle should change smoothly.
4. With the motors on and the platform still, it should not significantly different than with the motors off.
5. With the motors on and the platform moving, it should not significantly different than with the motors off. The zeros of the raw gyro measurement should align with the maxima and minima of the pitch angle.

The figure below illustrates the layers of filtering at their effect:

1. Top-left: The unfiltered accelerometer and gyro data (motors off). It is noisy, but note that the maxima of the accelerometer curve coincides with the zero of the gyro. This means the two signals are phase-aligned, since the gryo is the derivative of the accelerometer reading.
2. Top-right: The accelerometer data after the IMU's low-pass filter. The noise is gone, but it is out of phase and the amplitude is reduced.
3. Bottom-left: Combining the accelerometer data with the gryo data with the complementary filter preserves the smoothness and corrects the phase alignment.
4. Bottom-right: Turning on the motors doesn't affect the output of the complimentary filter.

Designed output

### Tuning Tips

Neither the complimentary filter nor the IMU's filters are sufficient on their own to get what we need: A smooth, non-drifting pitch angle in the presence of motor noise. It will take some trial and error to get the right output. Here are some tips:

1. Our gyroscopes are quite accurate, so integrating doesn't cause very much drift. They are also somewhat immune to vibrational noise. This argues for a high complementary gain.
2. The accelerometer has no drift, but is extremely susceptible to vibrations. This argues for a low cut off frequency for the accelerometer. This is ok especially because the gyroscope will provide good high-frequency data.
3. If your complimentary gain is too high, your measurements will drift. The drift can be very, very slow, but so take time to make sure it's not there.

You'll need to experiment quite a bit to get good measurement. The more tuning you can do without recompiling, the better, so spend some time refining your remote control code so you can tune things with the knob.

## Part II: Implementing PID

You will write the software to stablilize the FCB's yaw and pitch axes.  You should be able to control the following:

1. The spin rate of the FCB hanging from monofilament.
2. The pitch angle of the FCB on your test stand.
3. The overall thrust of the motors (using the throttle gimbal of your remote).

Using the yaw stick you should be able to easily control the rate of rotation of the quadcopter.  It should start and stop spinning quickly.

So you should be able to move your pitch gimbal and see the test platform quickly and stably move in response. 

For both pitch and yaw, you should should also be able to turn the throttle up and down without observing much change in the pitch angle or spin rate.

### What Should be Simple and What Should be Complex

Your implementation of PID should not be complicated.  The PID algorithm is not complex, and simple, straightforward translation of the math into C code works just fine.  The same goes for the complimentary filter.

My reference implementation of one PID controller is 5 lines and 252 characters.  There are no tricks in the code.  It is a direct transcription of the PID equation into C.  You just need to implement the math carefully and correctly.  My implementation of the complimentary filter is equally simple.  Simplicity here is a real virtue.  

This is not to say that the lab is easy.  It is not.  Debugging simple code can be quite hard -- all the more when the bugs will manifest themselves as a crashing quadcopter.  Tuning the PID loop is tricky, time consuming, and frustrating.  This source of difficulty is reflected in the reference design:  While my PID implementation is short and sweet, the code that allows me to quickly and easily tune my filters and PID coefficients from my remote is several hundred lines of code, contains some pretty tricky parts, and represents many more hours of my life.

In most (and possibly all cases), the solution is not in more complexity in your control code.  It is in more careful debugging, simplification, and careful, methodical testing.  That, and making sure that your battery is adequately charged.

### The Control Loop

You will implement two controllers in the lab:  one for yaw and one for pitch.  Your quadcopter will eventually have a third controller for roll.

The PID controlled is a closed loop controller. Here's the flow chart for a generic closed loop controller.

Closed loop

The "System" is your quadcopter. The "controller" is your PID code. The "input" is the target "angle of attack" or "rate of spin" for your quadcopter (0 means flat and not spinning).  This is also called the "set point" because it is what you want to set system to do (e.g., setting a thermostat).  The "output" is estimate of the quadcopter's pitch produced by your complementary filter and the yaw provided directly from the gyroscope.

The controller takes the difference between the desired state of system (input) with the current state of the system (output) as the "error."  Based on this error (and it's behavior over time), it computes a set of control setting (i.e., power levels for the motors) that will, hopefully, reduce the error.

You'll need to calculate the setpoint based on the position of your yaw and pitch gimbals.  For yaw, +/-180 degrees/sec is a good starting range.  For pitch, +/-10 degrees from horizontal is a reasonable range.  That is enough to make your quadcopter move forward or backward at a reasonable speed.

### The Mixer

The mixer (which would be inside the "system" box in the diagram above) is responsible for combining the current throttle setting with the outputs from the controller to set power levels for the motors.

A key consideration in the mixer is that the total angular speed of the propellers needs to remain constant.  That means that if you increase the speed of one counter-clockwise propeller you must decrease the speed of another one by the same amount.  This explain why propellers that are diagonally opposite one another rotate in the same direction.

The simplest way to implement the mixer is something like this: `power = throttle + PID_output` for the front motors and `power = throttle - PID_output` for the back motors.  A potential problem is that the PID adjustment might be larger than the current throttle value or the throttle value maybe very close to the max motor power. In both of these cases, the quadcopter will not be able to completely implement the output of the PID control. 

Initially, you can ignore this problem: Test with your throttle in the middle or so.  You may need to compensate for this problem later, or you may not.

For your real quadcopter, your mixer will need to account for inputs from all three PID controllers (Pitch, Roll, and Yaw).

### The PID Controller

The basic form of the PID controller is this (thanks Wikipedia):

PID Equation

Where:

* Kp, Ki, and Kd are the P, I, and D coefficients.
* e(t) is the error at time t.
* u(t) is the "control variable" (I.e., the adjustment you will apply to the motors)

Implementing the PID controller requires you computing the integral and derivative of e(t), and there are pitfalls in both of them.

#### The Derivative of Error

The easiest way to compute the derivative is by dividing the change in error by the change in time. Just remember:

* Measure time in seconds.
* Be sure you have the sign right on e(t) and de/dt. If you get it backwards nothing will work.
* Use the actual elapse time since your last measurement.

#### The Integral of Error

This one is a little trickier. The obvious answer is to just sum the error term forever. The problem here is that if you happen to hold your test platform steady with your hand, the integral will grow rapidly. 

For instance, if you hold it in a position where the error term is positive for 10 seconds, the integral term will come to a large positive value. When you release the platform, the platform will move sharply to a position with negative error (because it has been trying for 10 seconds to reduce the positive error). It will then take a while (maybe another 10 seconds) to “unwind” the integral by adding in the negative error.

Another common problem:  If your Ki = 0, and the integral of error becomes large (which is just what you would expect to happen when Ki = 0), and then you increasing Ki, your quadcopter will massively overadjust. 

There are couple of solution to this:

* You can have the integral decay over time.  For instance, instead computing `sum = sum + e` each iteration, you could do `sum = 3.0*sum/4.0 + e`.  The downside of this is that it will make your kI term's behavior more complex.  Complexity is your enemy.
* You can also just bound the integral at some value. Some trial and error may be required to find a reasonable bound.  Same problem as above -- this introduces a discontinuity is the algorithm's behavior.
* You can reset the integral when throttle is 0 or when `Ki` is zero.

You might also want to implement a "deadband" on throttle, so that if the throttle is below some small value, it reads as 0.  If your throttle is at 1, your motors probably won't turn on, but it would keep your error integral from reseting if you implement the last item above.

### Implementating PID

The PID algorithm is pretty simple and no complex tricks are required to get it to work.  That does not mean it's easy, though.  The big challenge is that it involves several interacting pieces: 

#### The IMU and your Filters

The PID controller does not control actually try to control the orientation of your quadcopter.  Rather, it tries to control the output of your complimentary filter.  If the filter's output does not accurately reflect the orientation of the quadcopter, all is lost.

You need to pay close attention to the output of your IMU and the complimentary filter.  For instance:

1.  Is the measurement accurate?
2.  Does track reality quickly and accurately? (your quad copter must react at sub-second time scales, if it takes 5 seconds for your pitch angle estimate to converge, the quadcopter cannot react faster than that.)
3.  Is there any clipping?
4.  Is there a lot of noise?

One particularly useful tip:  Don't worry about stability at low throttles settings.  I get horrible harmonic noise in my accelerometer at moderate throttle settings.  It's impossible to filter out, but the throttle is too low to take off at that level, so it's unimportant.

#### Your PID Implementation

The implementation can (and should) be pretty simple.  Trying to tweak the algorithm by having it behave differently in different situation, etc., is a recipe for poor performance.  Even without special cases, there are many simple errors to avoid.  Keep you code simple, clean, and well-organized.  If you code is a mess, and you have a sign wrong somewhere, you'll never find it.

If you get strange behavior, make your implementation simpler rather than more complex.

Pay attention to your PID update rate.  100Hz (10ms/iteration) is good.  The call to lsm.getQuad() takes about 1.8ms.  You will eventually have 3 PID loops. So that means you have about (10-1.8)/3.0 = 2.7ms per PID channel.  If you implementation is simple, this should not be a problem.

#### Your Mixer

The output of your PID controller is number that specifies how adjust the relative power of the front and back motors.  If that variation can't happen (because your motor outputs are saturated), PID cannot possibly work.  Implementing the PID's will is actually more important that implementing the pilot's requested throttle level (although you should strive for both).

#### Debugging and Tuning

* Use the knobs and buttons on your remote to tune parameters.  It’s much faster than recompiling.  Spending time on the code to support this will pay you back many times over.
* Use Arduino’s serial plotter to debug. You can put all sorts of stuff on there: Coefficients, the values of individual terms, etc.
* Start by just implementing an P controller (no I or D).  This should get you an oscillating test stand (for pitch) and spinning (for yaw).
* Save your PID parameters in the EEPROM.

When you encounter a problem in this lab, it really pays off to be methodical about how you track down the underlying cause.  Here is what I recommend as a check list:

0.  How's your battery?  If it's low, you'll have trouble.
1.  Are you controlling the right motors?  If the 2x3 SPI programming header is "front" of the FCB, the pins are: front-left: pin 4; front-right: pin 3; back-left: pin 5; back-right: pin 6.
2.  Do you have the right props on?  Make sure they are all blowing air down and that thy are turning the correct direction.
3.  Are you motors installed properly?  Diagonally opposite motors should have the same wire colors (i.e., red/blue motors should be on opposite corners).
5.  Check your raw IMU measurements -- are they reasonable?
6.  Is the sign of your pitch and roll rates correct (i.e., when the pitch rate is positive, is pitch increasing)?
7.  Check your filtered IMU measurements -- are they not-so-noisy when the motors are on?
8.  Is your IMU calibrated correctly?  When it's sitting on a flat surface or "docked" on the test stand, does it show 0-degrees pitch and roll and 0 yaw rate?
9.  Check your error calculation -- Does it change correctly when you tilt the FCB?  Does it change correctly when you move the pitch stick?
10.  Do the motor outputs change as you expect as you move the platform (i.e., do the motors on the lower side get stronger)?  Do they get stronger more aggressively when you turn up kP?
11.  Does it behave sensibly with just P?  Can you feel it trying to correct in the right direction?
12.  Check your derivative calculation -- Does it match up with your error calculation?  Is `dT` in the right units (i.e., compute using the right time scale)?  Does `dErr` have the correct sign (i.e., when error is positive and decreasing is `dErr/dT` negative?  When error is negative and increasing, is `dErr/dT` positive?)
13.  Does it behave sensibly with P and D?  Are your kD and KP reasonable values?
14.  Check your integral calculation -- Do you handle wind up correctly?  Is `dT` in the right units?
15.  Does it behave sensibly with PID? Is `kI` a reasonable value?

Almost always, overall PID problems are caused by something pretty early in this list.  It would be not be a bad idea to provide the means to run these tests quickly using the remote.  Then, if you have an error, you can quickly check whether all the underlying parts are working properly.

Be assured that the first time you ask me or the TA for help, we will go through this list (or something like it) with you.  You can save us both time by checking these items yourself first.

Here are some implementation notes suggested by the above:

1.  It'd be useful to have a mode where you can easily turn on one motor at time.
2.  It's useful to have a "manual" mode where your pitch stick directly controls the differential in power between the front and back props.  Might as well add left and right (for roll) and clockwise/counter-clockwise (for yaw).
3.  It's useful if the logic to disable the motors when the quad is disarmed does so at the last possible stage.  Then you can watch what sense/filter/PID/mix datapath is doing while the quad is disarmed.  It's very hard to concentrate on debugging when your quadcopter is flopping around.

#### Interpreting Your PID Parameters

As you tune and debug, you should think about what the value of each of your PID coefficients means.  This will help you tell if the values you are using make sense, and that will give you insight into whether your code is correct.

To make your PID coefficients easier to interpret, it is critical that you be calculating the derivitive and integral terms properly.  In particular, you need to calculate the derivitive by dividing the change in error by the change in time _in seconds_.  Likewise, you need compute the integral by summing the error times the change in time _in seconds_.  Remember, `millis()` gives you milliseconds, not seconds.

The P term controls how your quadcopter responds to error (measured in degrees).  Practically, this means that if P = 1 and error = 1 degree, than you are going to be changing your motor output by about 0.39%  = 1 * 1/255.  You can use this observation in several ways: 

1.  Check whether your motor outputs actually change by that amount when the error = 1 degree (or some other known quantity).
2.  You can experiment to see how big a change in motor output is required to change the orientation of the quadcopter on the test stand.
3.  If you need very large P values (e.g., P = 100) to get significant movement, something is wrong.  That means that a 1 degree change in orientation would result in 1*100/255 a 50% change in motor output.  

You can apply similar to reasoning to the D term.  The error derivitive is measured in degrees/second, and if you aren't moving your gimbals, it's just a measure of how quickly your quadcopter is rotating.  If error is change by 45 degrees/second and D = 1, then it will cause a 45/255=17% change in your motor output.  Experiment with your test stand to see how fast or slow 45 degrees per second is.  Does a 17% change in thrust seems like a reasonable response to rotating at that rate?

### Utilize the Bottom-Entry Programming Header

The programming header on the FCB can accept the programming cable from the top
or the bottom (fancy, no?  Well, maybe not. It can be a little flaky.).  Attaching the underside can be helpful to get the
programming cable out of the way.

### Trim

The calibration of your IMU is never perfect, and you will probably find that your quadcopter tends to drift/flop to one side.  Adding a trimming mechanism can help with this.  "Trimming" means adding a small, fixed offset to the controls (or the sensor readings) that can be adjusted in real time from the remote.  The D-pad of buttons is great for this.  It needs to be very easy to use -- it's not unusual to adjust trim while the quadcopter is airborne.  You probably only need to trim pitch and roll, and the D-pad is very intuitive for them.  If you want to be able to trim yaw as well, use the knob.

### The Yaw Axis

The yaw axis is the easiest of the three, so you should start there.  It's easy
becuase it doesn't move very fast and changes in the yaw angle don't cause the
quadcopter to move like pitch and roll do.

The first challenge is how to let the quad spin freely.  I've found the best
way to do this is to use monofilament to hang the quadcopter from the four
dowels we povided.  The real trick, though is to hang it upside down:

Hanging Quad for Yaw

If you mount it right side up, it'll try to take off and start flopping around.
Flying it upside down means the harder you drive the motors, the more stable it
gets in the pitch/roll directions.  Just keep in mind that it'll look like it's
spinning backwards relative to what you do with the yaw stick.

To let the quadcopter spin freely, we have "spinners".  If you put it between your quadcopter and
whatever it's hanging from, it'll let the quad spin freely without twisting the
monofilament.

I recommend the Kreh Loop (https://www.netknots.com/fishing_knots/non-slip-loop-knot) to tie your monofilament to the wooden dowels.  It will create a small loop that will not close when you remove the monofilament from the dowel, so you can slip it back on again later.  The improved clinch knot (https://www.netknots.com/fishing_knots/improved-clinch-knot) will work also.  It is a good choice for tying monofilament to the 'eye' of the spinner.

The PID loop is different for yaw than it is for roll and pitch: Rather than
controlling the yaw angle, you are controlling the yaw rate.  This means can
just use the gyroscope output directly.  Neutral on the yaw stick should
correspond to a yaw rate of zero.

The behavior you are looking for is crisp start and stop of the rotation when
you move the stick and return it to neutral.  You should also be able to feel
it fight you if you try to rotate it by hand.

You want the lowest PID coefficients that give good results.  If they are too
high, I find the quadcopter will overreactive to small yaw distrurbances while
flying.

A few things to watch out for:

1.  You may notice some wobbling on the pitch and roll axes.  This is fine and seems to be a product of it being constrained and upside down.
2.  Make sure your gimbals are calibrated so that the neutral position on the yaw stick corresponds to a yaw rate of zero.
3.  Make sure your IMU is calibrated correctly.  It's easy to accidently calibrate the IMU while the quad is spinning slowly in the air.  This will make it impossible for you to achieve zero yaw and a neutral yaw stick position.
4.  The trim mechanism is useful for testing.  It will let you set the yaw rate so you can vary the throttle while maintaining a constant yaw rate, which is a good way to verify that your PID works across throttle values.

### The Pitch Axis

Tackle the pitch axis next with the quadcopter on the test stand.  This is
where you will probably spend most of your time.

The behavior your are looking for is stable, level "flight" when the pitch
stick is at neutral.  Ideally, you'll you see crisp responsive movement as you
move the pitch stick.  It should also me symmetric -- moving the stick forward
should have the opposite effect as moving it backwards.

Again, you can use the trimming mechanism to demonstrate stable operation across throttle values.

### Tuning Resources

Much has been written about how to tune PID controllers. I have used these two techniques with success:

* A simple manual tuning algorithm: https://en.wikipedia.org/wiki/PID_controller#Manual_tuning
* A more disciplined heuristic algorithm: https://en.wikipedia.org/wiki/PID_controller#Ziegler%E2%80%93Nichols_method

### Resources and Examples

#### Resources:

1. https://en.wikipedia.org/wiki/PID_controller
2. Interactive demo: https://sites.google.com/site/fpgaandco/pid
3. Cool example: https://www.youtube.com/watch?v=j4OmVLc_oDw

### Turn in Your Work

Commit your results:

1. Commit an updated version of `quad_firmware.ino` and `remote_firmware.ino`.

#### Demo your work:

1. Demo your clean orientation measurements for the TA.
2. Complete the reflection for this lab: https://docs.google.com/forms/d/e/1FAIpQLSfB8XsDV8FtTZYO1mv3FZrd9mUs1hDlFvQxnfAK0K2zptTjxQ/viewform

### Rubric

For the demo be ready with the serial plotter showing the output of your complimentary filter and the raw gyroscope output. Those are the only signals we need to say to grade the lab.

Possible points: 10

Check list

1.  Motors off, Quadcopter horizontal, your filter outputs should be zeros (1 point)
2.  Moving the motors manually should show smooth output of the filter (1 point)
3.  Quick movement of the FCB should show quick response from filter output (1 point)
4.  Phase alignment should be good (gyro zero matches angle maxima/minima) (2 points)
5.  All of the above must hold at with motors at 75% throttle (5 points)

You will lose one point for each day late your solution is.

Possible points: 13

Check list (for each axis):

Yaw:

1. Non-spin with yaw neutral.
3. No visible oscillation
4. Trim functional.
5. Crisp, sharp start and stop.
6. Constant yaw rate with increasing throttle.

Pitch:

1. Level "flight" with pitch at neutral.
2. Only moderate oscillation at neutral.
3. Almost no oscillation at neutral.
4. Trim functional.
5. Symmetric movement pitching forward and back (pitch stick at 10degree position gives 10 degree tilt)
6. Same amount of oscilation when pitched as when level.
7. Moderate overshoot
8. Almost on overshoot.

You will lose one point for each day late your solution is.

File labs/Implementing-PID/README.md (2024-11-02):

# Implementing PID

To be completed in your groups.

Check the course schedule for due date(s).

## Skills to Learn

## Equipment, Supplies, and Software You Will Need

1. Test stand
2. Remote control

### Turn in Your Work

#### Commit your results:

1. Commit an updated version of `quad_firmware.ino` and `remote_firmware.ino`.
2. Updated version of `noise.txt` with updates filter configuration parameters
   (if you changed them), and the your PID and values for each axis.

#### Demo your work:

1. Demo your clean orientation measurements for the TA.
2. Complete the reflection for this lab: https://docs.google.com/forms/d/e/1FAIpQLSfB8XsDV8FtTZYO1mv3FZrd9mUs1hDlFvQxnfAK0K2zptTjxQ/viewform

### Rubric

Possible points: 13

Check list (for each axis):

Yaw:

1. Non-spin with yaw neutral.
3. No visible oscillation
4. Trim functional.
5. Crisp, sharp start and stop.
6. Constant yaw rate with increasing throttle.

Pitch:

1. Level "flight" with pitch at neutral.
2. Only moderate oscillation at neutral.
3. Almost no oscillation at neutral.
4. Trim functional.
5. Symmetric movement pitching forward and back (pitch stick at 10degree position gives 10 degree tilt)
6. Same amount of oscilation when pitched as when level.
7. Moderate overshoot
8. Almost on overshoot.

You will lose one point for each day late your solution is.

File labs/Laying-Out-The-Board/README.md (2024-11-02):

# Laying Out the Board

To be completed in your groups.

Check the course schedule for due date(s).

## Skills to Learn

1. Layout out a complex board.
2. Build power and ground planes.
3. Work with layers to control routing.
4. Size traces correctly.
5. Use the autorouter.
6. Protecting analog components from interference.
7. Drawing a logo in Fusion360.

## Equipment, Supplies, Virtues, and Software You will Need

1. Fusion360
2. The contents of QuadClass-Resources repo, as well as `quadparts_prebuilt_2022`.
3. Patience.
4. Attention to detail.
5. Read through the [Fusion Tricks Page](../../Fusion-Tricks.md) and skim the [Autodesk docs](https://help.autodesk.com/view/fusion360/ENU/?guid=ECD-PREPARE-LAYOUT) that go over the design tools you will use this lab.

## Tasks To Perform

### Board Shape and Quadcopter Orientation

The first step is to define the size, shape, and orientation of your quadcopter. There are several things you must take into account:

1. You need places to attach four motors. We will use rubber grommets to attach the motors to your PCB just like we use them to attach the motors to the FCB's airframe. However, the grommets that fit on the PCB are much smaller. You will need a hole that is 12.2mm in diameter for each grommet, and the ring of PCB around the grommet must be at least 1.7mm wide.  You should use circles in the `Dimension` layer rather than the "hole" tool to create these openings.  "holes" are drilled and these openings are too large to drill.
2. You should ensure that most of the area the propellers will sweep out as they spin will not be over the board. For instance, putting the motor at the end of an arm will accomplish this. The arm must be long enough, however. The diameter of the propellers is either 40mm or 65mm. Design for 65mm. You can add four `PROPELLER` devices to your schematic/board to see this in your design.
3. Your design must fit with a rectangle whose area is less than 19,354 sq mm. -- about 13.9cm square. This is pretty big. Don't feel the need to fill it. Heavier quadcopters are harder to get off the ground.
4. The layout of the motors should be symmetric along the the x and y axes (i.e., the four motors should make a rectangle).
5. I recommend centering your board shape on Fusion360's origin. It will make it easier to place parts symmetrically.
6. The cutting tool the board uses is a 2mm in diameter. This means if you should corners that are less than 180 degrees (i.e., the corners point into the body of your quadcopter), they will be rounded.
7. The cutting tool diameter also limits the smallest gap between two the board and itself. Openings must be at least 2mm wide. You can get a feel for this by doing `hole 2mm` which will give you 2mm circle that you can slide use to guage how the cutting tool will behave.
8. The board manufacturer will not build boards with "ismuths" (i.e., narrow strips of PCB) narrower than 2mm. The guidance they give is not totally clear, but protrusions (i.e., pennisulas) seems to be OK, while narrow strips between larger parts are not. If you want something unusual, we can always send it in and see what they say.

To verify that you have the dimensions correct, please add dimension elements to your board in `tDocu`. You need these four dimensions (all in mm, of course):

1. The width of your board at its widest point.
2. The height of your board at its highest point.
3. The diameter of the opening for your motors (should be 12.2mm). You can also do the radius.
4. The thickness of ring surrounding your motors.

### Configure Fusion360

We will be building 4-layer boards. You’ll need to set up Fusion360 for this. Here are the steps:

1. Select `Rules DRC/ERC->DRC`
2. Load `pcbcart-4layer-5mil-small-cream.dru`. Use this DRU file for the rest of the project.

### Place the Parts

The next stage is to place all the parts on board. Placing most of the parts is straightforward. Here are some things to keep in mind:

1. The location of some components is more important that others. Place these first and use them to guide the overall layout.
   1. The motor controllers should be close to the motors, so the wires on the motors wil reach the motor connectors. The connectors should be no more than 45mm from center of the motors.
   2. The reset button and the battery connector should be out from under the propellers, so you don’t injure yourself while trying reset or unplug the quadcopter.
   3. The power switch is meant to be on the edge of the board (see image below). It also needs to be reachable when the props are moving.
   4. There needs to space on either the top or the bottom for the battery. There should be a roughly flat area (like there is on the FCB).
   5. The IMU should be at the center of your quad.
   6. Any other LEDs you added should placed in an artistic way (or to achieve whatever effect you are going for).
   7. The 4-pin programming header should be well-away from the propellers.
   8. The location of the micro-controller is not, in itself, important, but it’s location does drive the location of the antenna and the crystal.
   9. The antenna needs to be close to the edge of the board and it needs a fair amount of metal-free space around it.
2. You should mimic the layout of the FCB in places where signal integrity is important. This includes antenna (see below) and the crystal.
3. Make your board look good! Align components that are next to each other, make the spacing between components consistent, etc. Board designers appreciate a good-looking board.

Power switch

### Board Layout Style Guide

Eaglint will warn about most of these.

1.  Align your parts to a 1mm grid. This will go a long way toward making your board look really good. The antenna and the capacitor attached to it don't need to be on the grid, because signal integrity is more important. You can also bend the rules and use 0.5mm grid for placing caps need the IMU and MCU. Eaglint enforces the 0.5mm grid. If you have good reason violate the grid, you can explain it in Eaglint.
2.  Align your reference designators and values to a 0.5mm grid. Sometimes this is too restrictive. If you must, you can use 0.1mm. Eaglint will complain otherwise.
3.  Allow 1-2mm between parts to make assembly easy. If you designed your `tKeepout/ComponentExcludeTop` appropriately in the library, this should be no problem.
4.  Orienting all your parts in the same direction makes assembly easier (notice this on the FCB and your remote board).
5.  To be legible, any silkscreen text needs to be at least 0.9mm high, with a 'ratio' of 8%. You should use the `vector` font. Eaglint forces you to use exactly these settings on the reference designators.

Boards don't typically include the values of each component, but we do because it makes assembly easier.

### Logo and Decorations

Your team should have a logo! Design it in the footprint editor and then create a device called `DECORATIONS` in the `custom` library that contains it. You'll need to create a symbol to go along with your new logo, which can just be a box with a `>name` and `>value`. The name of the variant should be descriptive of what the decoration is, and feel free to add as many decorations as you like! You can see an example of the `DECORATION` device in the `quadparts_prebuilt` library.

You may need to generate different versions with different sizes (there’s no way to scale anything in Fusion360). If you want to get creative, you can integrate solder mask, silkscreen, and metal into your logo design. Checkout the quadcopter logo on the FCB, remote, and battery charger boards: It uses exposed metal, metal-under-mask, and silksceen.

### The Power Supply

To power your quadcopter, you need provide ample current to the motors and clean 3V power to the microcontroller and IMU. The vast, vast majority of bugs I encounter in PCBs like you quadcopter have to do with the power supply.

The power supply for the quadcopter is complicated because we have two different power systems that have different requirements: The motors need maximum power — high current and high voltage — while the IMU and microcontroller, need a clean, regulated, consistent voltage and don’t require much current.

To do this you will need to carefully layout the battery, the voltage regulator, and the bridge between `BAT_GND` and `GND`. You will also need to create a set of "pours" to efficiently regulated and unregulated power to the components that need it.

You have already built your schematic to provide separate power and ground nets to these two sets of components. Now we are going to exploit that separation to physically realize two, mostly separate power distribution systems that will meet these needs.

You have four signal layers (Top, Bottom, and two internal layers). The two internal layers will be a power and ground plane — i.e., dedicated to delivering the power and `GND` signals across the board. These layers are, for the most part, filled with metal. To create these metal areas, you will create pours.

For the 3V power supply (`3V` and `GND`) here are the key considerations:

1. We need to isolate them from the high-voltage supply, both physically and electrically.
2. We need to provide adequate “decoupling capacitance” to minimize noise due to digital switching.
3. We need to provide low-resistance path between the component and `3V` and the components and `GND`.
4. Correctly layout the voltage regulator according to the guidance in the datasheet.

For the high-current supply (`VBAT` and `BAT_GND`), here are the key considerations:

1. Minimize resistance between the battery and the motor drivers.
2. Minimize resistance on the nets within the motor driver.

#### Basic Principles: Resistance

The resistance of your power and ground connections is important because resistance causes voltage drop. The voltage drop, `V`, for a current, `I`, flowing through a given resistance, `R`, is given by [Ohm’s law:](https://www.electronics-tutorials.ws/dccircuits/dcp_2.html) `V = IR`. Power distribution systems carry non-trivial amounts of current so, the voltage drop can be significant.

Our power distribution networks are made of the copper foil that makes up the traces on our PCBs. Resistance for a sheet of copper (or any conductor) is proportional to sheet’s aspect ratio. Long, thin wires have higher resistance than short, fat wires. For this reason, sheet resistance is measured in Ohms/square: A square sheet of copper has the same resistance, regardless of its size.

You can calculate the resistance of a wire on PCB using [an online calculator](http://circuitcalculator.com/wordpress/2006/01/24/trace-resistance-calculator). Our wires are 1oz copper. For instance, a 50mm wire that is 6mils wide has a resistance of 0.127Ohms. If you tried to power one of your motors — which can consume over 2A — using such a wire, the voltage drop would be 0.24V or about 6% of motor power. Not the end of the world, but still a waste.

The way to minimize resistance is to make wires wider: Increasing the width to 2mm, reduces the resistance to 0.01Ohms or so.

#### Basic Principle: Inductance

The second principle you need to consider is inductance. Inductance is a resistance to change in current. The mathematics are more complicated than they are for resistance, but intuitively, if you suddenly turn on a transistor (i.e., the mosfet in your motor driver or the millions of transistors in your microcontroller), it takes a little while for the current to start flowing. Likewise, if you turn off a transistor, it take a little while for the current to stop flowing (this is what caused flyback in our motor driver).

There’s a calculator for PCB trace inductance [here](http://chemandy.com/calculators/flat-wire-inductor-calculator.htm). The equation is more complex than Ohm’s law, but the trend is similar: Longer, thinner wires have higher inductance. This resistance to the change in current, can also cause a voltage drop along a wire — the higher the inductance, the larger the drop. Calculating the actual voltage drop is a little complicated because you need to to know the rate of change of the current (dI/dt). You could use one of the oscilloscopes in the maker space to do this for your motor drivers, if you wanted. The important thing, though, is that `dI/dt` is high in our boards, so inductance is a problem.

Conveniently, minimizing inductance and resistance both push us toward making the wires in our power supply networks as short as possible and as wide as possible.

### Building Power and Ground Planes out of Pours

PCBs provide an easy way to minimize inductance and resistance while maximizing capacitance in our power distribution system: Power planes. Power planes are entire layers of your PCB dedicated to power or ground. They cover all or most of the PCB and the power and ground planes should overlap as much as possible. This provides:

1. Low resistance and inductance because they planes act as very wide wires.
2. Capacitance because the power and ground planes form two plates of a capacitor.

We will build the power and ground planes out of "pours". To create a pour, use Fusion's polygon tool.

1. Select the tool and the select the layer you would like the pour to be in. In your case one of the internal layers.
2. Select the area you would like the pour to include. There is a "width" option you can set while drawing the outline. This corresponds to the width of the outline. I recommend using a small value (e.g., 0.5mm).
3. Select the `Name` tool (Or type "name" in the command line) and click on an edge of the polygon. Type (e.g., “GND” if the metal should be connected to GND). It may ask if you want to merge nets (yes), what the resulting name should be (e.g., “GND”), and/or whether you want to rename the whole net or just this polygon (just the polygon).

Once the pour is created, you can click the "Show all polygon pour fills" tool and Fusion360 will fill in the pour. Fusion360 is intelligent about how it fills in the pour. It will carve out areas around pads, SMDs, and traces that are part of the signal assigned to the pour. For pads, SMDs, and traces that are part of the same signal, Fusion360 will attach the pour to those components.

You can also extend the pours past the edge of your design. Fusion360 will trim them to match your board shape. This much easier than following your board's shape with the polygon.

The gaps and holes Fusion360 can divide the pour into multiple pieces that are not directly connected to each other. By default, Fusion360 will not fill in a pour fragment if there is no connection to the pour’s signal. The unconnected pieces are called “orphans”.

To see the gaps Fusion360 will create in the pour, the connections it will make to pads and signals, and which portions of the pour are orphans, you can click "show all polygon pour fills" from the "polygon tool palette. If nothing happens, that usually means that no part of the pour is connected to the signal, so the entire thing is an orphan.

The easiest way to ensure that the pour is connected to its signal is to add insert a via in the pour. You can do this with `Via` tool. Select it, make sure it’s set to insert a round via and add one to the pour near the edge. Use the `Name` tool to set the signal for the via to the pour’s signal name. Alternately, you can type `via '<pour signal name>'` in the command line and then insert a vias by clicking. Select "Re-fill polygon pours", and the pour should fill in.

To unfill the pours (they can make it hard to see things in your design), you can type `ripup @;` in the command line or click "hide all polygon pour fills".

#### Design Your Power and Ground Planes

In our design, we have two power supply signals ( `VBAT` and `3V` ), so we will use two power planes in layer 15. How exactly they should be configured will depend on your design, but one reasonable way to start is to draw a polygon around the perimeter of the board (shaped like a “C” if your board is round). It should be no narrower than 4-5 mm at any point. It should pass under all four of your motor drivers and it should also extend to any area where your battery connector and voltage regulator are located. This will let all these components connect directly to the pours, avoiding long, thin, high-current wires.

The `3V` pour should cover the rest of the board (except around the antenna. See below). Set the net for that pour to `3V`.

There should should be a corresponding ground pour above these two pours (on layer 2). The `GND` pour should be same shape as the `3V` pour, and the `BAT_GND` pour should be the same shape as the `VBAT` pour.

Note that none of these pours should form a complete ring or "donut".

The top and bottom layers should have a single, large pour of `GND` that covers everything except the area around the antenna.

Ideally, your pours should not have sharp (90-degree) corners, since it leads to "current crowding". This is not a big deal in our designs, but it is an interesting phenomenon (https://www.signalintegrityjournal.com/blogs/6-expert-advice-on-power-integrity/post/534-the-perils-of-right-angle-turns-at-dc).

You should also be careful that your power planes on layers 2 and 15 are not cut in two more pieces by traces routed through them. The goal is to have the pours provide a nice, wide, low-resistance path to the battery, the voltage regulator, the battery, or the net bridge (depending on the pour). If it's cut in to pieces, all but one of the pieces will usually be connected by a single trace instead.

You can check whether your power planes are not sliced up you can do `display none 15` or `display none 2` to look at just those metal layers. `display all` will show everything again.

You should also pay attention to the narrowest point on your `VBAT` and `BAT_GND` pours. We want wide wires all the way from the battery to the motors, if there's a narrow spot that can significantly increase the resistance. We are interested in width of the actual metal, not the polygon you've drawn. Pay attention for anything that might reduce the effective width of your pours (e.g., throughholes).

#### Exploiting Your Power and Ground Planes

The goal of the pours is to provide a low-resistance path for current to and from the battery, but they can only do this if your design uses them.

This means that, wherever possible, you should route your board to use the power and ground planes rather than traces. So, you want the traces that carry `GND`, `BAT_GND`, `3V`, and `VBAT` to be as short and as few as possible.

The easy way to do this is with the `fanout` command. It'll draw a short wire attached to each pad and put a via at the end. `fanout SIGNAL GND` will do this for all your ground pins. The `fanout` command is imperfect, so may have to fix up its work.

It also makes sense to shape your power and ground planes so that the planes are available where the signal is needed. This is why `VBAT` and `BAT_GND` should extend under all the motor drivers the battery connector.

If Eaglint complains about trace length on high-current traces, you can offer an explanation about traces to LEDs and the breakout header.

#### Laying out the Power Supply

There are three reasons that these components need to be close together:

1. The battery connector needs to be close to the voltage regulator to minimize the length the high-current trace between them. Just a few mm’s away.
2. The wire bridge needs to be close to the battery’s negative terminal to minimize the length of the trace connecting them. Again, a few mm’s.
3. The capacitors for the voltage regulator need to be as close as possible to the regulator because the datasheet says so.

Section 10 of the voltage regulator data sheet has detailed instruction for layout your power supply. Follow them as closely as possible. Your 0805 caps are not quite small enough to do exactly what they request, but you can come close. Eaglint requires the 1uF caps to be with in 5mm of the regulator, measured center-to-center. You can relax the grid to 0.5mm if needed -- just add a note explanation, if eaglint complains. The 47uF cap on the regulated side needs to be with 10mm.

Be sure that the decoupling capacitors on the output of the voltage regulator are close to the regulator, close to each other, and connect directly to the `3V` pour in layer 15 and all three `GND` pours (layers 1, 2, and 16) through vias situated close to the capacitor's SMDs. You also want the traces from the capacitor terminals to the voltage regulator to be as short as possible.

Simultaneously satisfying all these constraints will require careful thought and planning. In particular, these constraint will affect how you layout the power and ground pours.

The traces from the battery to the jumper should be in your high-current net class (see below) as should `BAT_GND` and `VBAT`.

The design includes a wire bridge that connects `BAT_GND` to `GND`. The reason for this is to ensure that noise from the motors (which are connected to the `BAT_GND)` does not impact the microcontroller. In order for this work, you need to place the bridge as close to both the battery and the voltage regulator as possible. This will ensure that the regulated ground has the shortest possible connection to the negative battery terminal.

### Laying out the Motor Drivers

To maximize thrust and responsiveness, you should keep the high-current (i.e., the mosfet, the motor pads, and flyback diode) components of each motor driver close together. `VBAT` should feed the into the controller directly from the `VBAT` power plane. Since the `VBAT` power plane is in Layer 15, and the pads are on Top, you’ll need at least one via, to connect the two. Consider using more than one via, to provide a wider conduction path. You can add all the vias you want using the `via` too. The `fanout` tool will also add vias for you.

The routing for the low-current components of the motor driver (i.e, the PWW line and the pull-down resistor) is less critical.

### Laying out the Radio

The radio is one of the delicate parts of the board because it require special attention for good signal integrity. You should copy the layout on the remote as closely as you can. The key things you’ll need to get right are:

1. You can ignore the grid requirements in placing these parts. Matching the reference design is more important. If eaglint complains, add a note of explanation.
2. Except for the pad that is attached to the circuitry, the antenna should be mounted near the edge of the board without any metal nearby (i.e., there should be no metal in any layer in that area). Note that on the remote, the antenna is on it's own protrusion of the PCB far away from any metal. You don't need a protrusion, but the lack of metal nearby is important.
3. The two capacitors and the balun that make up the antenna driver should not have any other signals near them.
4. The length of the traces from the micro controller to the balun should be as symmetric as possible: Equal length and mirrored geometry.
5. All the wires in the antenna should be as short as reasonably possible. This constraint, combined with the need for the antenna to be near the edge of the board constrains where you can place your microcontroller.
6. The wire between the balun, the antenna, and the capacitor between them should be the same width as the antenna (50mil), and the wire should transition smoothly into the antenna. There should be no sharp corners.

Enforcing all of these requirements will require applying multiple techniques. Begin by laying out the parts to match the layout on the remote. Then read on for tips on how to implement the rest of the requirements.

Just to drive home how delicate this part of the design is: I have here on my desk a package containing 25 remote control boards that have a range of about 4 inches because I got overconfident about how much I could mess around with the antenna layout. Don't do that :-(

#### The Antenna

Building good antennas and the circuits to drive them is a deep and interesting area of electrical engineering. It's also beyond the scope of this course.

To side-step that problem we are borrowing tested antenna design and layout. You can use the remote or FCB as a guide (the microcontroller is at the bottom the the antenna is at the top:

Antenna Layout

The antenna also needs a ground plane (https://www.electronics-notes.com/articles/antennas-propagation/grounding-earthing/antenna-ground-plane-theory-design.php). This is simply a large area of metal extending out from the base of the antenna. It's radius should be something 1/4 of the wavelength the antenna should emit. Four our 2.4Ghz radio, that's about 31mm. The ground pours in the PCB will work just fine (so you don't need add any additional metal to satisfy this requirement).

### Setting Trace Widths

By default, Fusion360 uses the narrowest wires allowed by the DRU file. For us, that’s 5mil (0.127mm). Narrower wires have higher resistance, and if a trace needs to carry a sensitive signal (e.g., to drive our antenna) or lots of current (e.g., to or from our motors), the trace will need to be wider.

Fusion360 provides the notion of ‘net classes’ to specify different characteristics for different signals in your design. We will define three new net classes.

To create or edit a net class, go to your schematic, select `VALIDATE->VALIDATE->Net Class`(You can also go to board file, selecet `RULES->PERFERENCES->Net Class`). If you want to create a new net class, click “Add” Button on the left bottom to add a class of net, give it a name, then choose nets from middle column, the chosen net will move from middle column to right column.

First, create a net class called “RFSIG”. “RFSIG” should include signals between the balun and the antenna. Note that wires beteween the MCU and the balun can be in the default class. The width of them should be ‘50mil’.

Second, create a net class called “PWR”. “PWR” should indule all 3V and GND signals The width of them should be ‘10mil’.

Third, create a net class called “HIGHCURRENT”. “HIGHCURRENT” should include all VBAT and BAT_GND signals. This net class is going to be for wires that carry current to the motors, but how wide should those wires be? This depends how much current the wire will carry, how hot we are willing to let it get, how large a voltage drop we can tolerate, how long the wire is, and how thick the copper is. The calculation for this are complex, but fortunately, there are tools online to figure it out for you. [This is a good one](https://www.4pcb.com/trace-width-calculator.html).

Our motors can draw about 2A, so peak current is something over 8 amps. The batteries we use can deliver up to 9.5. We are using 1oz copper (which means one square foot of the copper foil weighs 1oz. This works out to 0.035mm). 10 degrees Celsius is a reasonable rise in temperature. Room temperature is 25 degrees C. The traces will be pretty short — probably less than 0.5in (or 12.7mm).

These traces are probably going to be on the top or bottom layers (although you should check this is the case after you’ve routed the board), so we are worried about “external layers in air.” Given all that we, see that a trace 30mils (0.72mm) will work just fine.

Then slect `RULES->Design rules->Custom Rules->Copper Width` in board file. Click the ‘+’ button. In the “Scope” section, in ‘Object 1’ selcet "In Net Classes", then selcet the net class you want to assign. In the “Parameters” section you can enter the Minimum and Prefered, just enter our requiared width in both boxes. 

There will also be vias carrying these currents. We can increase the default via size for the next class to match the width of the trace. The diameter of a via is the drill size (which you can set in the `RULES->Design rules->Custom Rules->Drill Size`, same logic as trace width) plus an annular ring (which is the ring of copper you can see around the via). Our DRU file set the annular ring to be 25% of drill _radius_. Calculate a drill size that will give an annular ring diameter of 30mil and enter that value for the drill field for the “HIGHCURRENT” class.

Now that we have established the net classes, we need to apply them to some nets. This is easiest in the schematic view using the "Change" tool. If you click on the Change tool, you’ll get a list options, select “Class” and then select “HIGHCURRENT”. Then, go click on all the wires connecting components of the four motor drivers. You can skip the signals through the pull-up resistor, if you want.

### Laying out the IMU

You need to add some additional bits to the IMU package. You built your IMU package with rectangle in `tRestrict/RestrictTop`, `bRestrict/RestrictBottom`, and `vRestrict/RestrictVias` to prevent metal in the top and bottom layers, but there is no restrict layer for the internal layers. You will need to add a "cutout" to make sure there are the appropriate holes in in your `3V` and `GND` planes.

To create a cutout, use the polygon tool, and check the 'cutout' box in the properties dialog.

The IMU datasheet and a technical note provide guidelines for layout the IMU and its associated components. Follow them.

The caps for the IMU need to be as close to the IMU as possible, and the traces between the caps and the IMU need to be as short as possible. For decoupling caps, the length of the `3V` trace is most important. Eaglint requires all these caps to be with in 7mm of the IMU, measured center-to-center. You can relax the grid to 0.5mm if needed -- just add a note explanation, if eaglint complains.
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

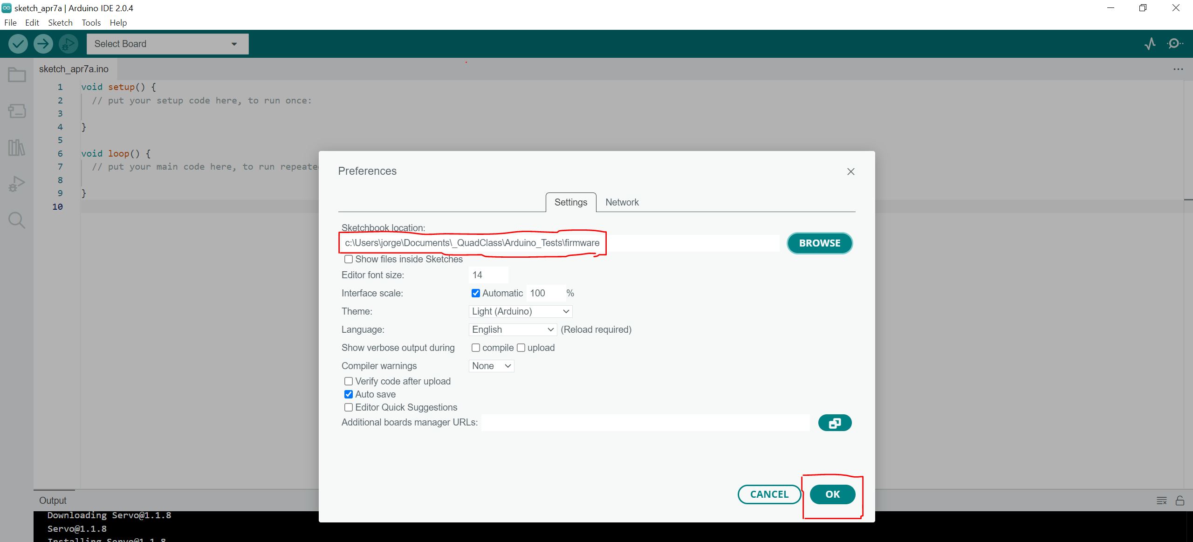
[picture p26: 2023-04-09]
labs/Programming-The-Hardware/images/introprog2.jpg

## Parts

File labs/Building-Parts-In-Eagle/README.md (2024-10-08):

# Building Parts in Fusion360

To be completed on your own.

Check the course schedule for due date(s).

## Skills to Learn

1. Learn to use the package generator in Fusion360.
2. Learn to create more complex, footprints, devices, and schematic symbols in Fusion360.
3. Learn to interpret device datasheets to ensure that the footprints you design meet the requirements of the devices they are for.

## Equipment, Supplies, and Software You will Need

1. Fusion360
2. The starter repo: for this lab: [https://classroom.github.com/a/_5sFMHYf](https://classroom.github.com/a/kOVXSXw8). (Don’t clone it until the start of class, last minute changes are likely)
3. Read through the [Fusion Tricks Page](../../Fusion-Tricks.md) and skim the [Autodesk docs](https://help.autodesk.com/view/fusion360/ENU/?guid=ECD-LIBRARY-DESIGN) that go over the design tools you will use this lab.

## Preliminaries

### Make Fusion360 Easier to Use

Set your grid to mm, you can follow the instructions [here](https://knowledge.autodesk.com/support/fusion-360/learn-explore/caas/sfdcarticles/sfdcarticles/How-to-Change-Units-in-Fusion-360.html).

A sample `eagle.scr` is available in this repo under `QuadClass-Resources/Eagle/eagle.scr` It will set the grids to the correct defaults in new schematics, boards, and libraries you create.

### Units of Measure

In a perfect world we would all use mm for everything when designing our boards. Unfortunately, this not always possible. Fusion360 uses mm internally, but for some reason it wants to use ‘mils’ for some parts of its UI and inches are the default in others. In addition, by convention, Fusion360 schematic symbols are built on a 0.1” grid. And some board houses specify tolerances in mils or inches.

This means you need to pay close attention to your units. Here’s a simple reference:

- 1 in = 25.4mm
- 1 mm = 0.0387... inches
- 1 mil = 0.001 inches

In Fusion360, the safe thing to do is write it out. If you type ‘1mm’ or ‘1in’ or ‘5mil’ into a length field in a dialog box, Fusion360 will do the "right" thing (namely convert it to whatever it wants to display and show that value).

## Building Parts

Create footprints, symbols, and devices for the following electrical components. You'll add these to a newly-created (by you) `lbr/custom.lbr` in the lab repo.

| Description | Digikey part number  | Notes |
| --- | --- | --- |
| 0805 0Ohm resistor | 311-0.0ARCT-ND | Build resistors by hand |
| Red Light emitting diode | 160-1178-1-ND | Orientation is key <br/> Use the package generator for the LED |
| N-Channel MOSFET | SI2302CDS-T1-E3CT-ND | Pay close attention to the pads <br/> Use the package generator with a custom footprint for the MOSFET (or build by hand) |
| LSM6DSOXTR 6-Axis IMU | 497-18367-1-ND | The package generator doesn't support this IMU, build the footprint by hand |

You can find information about the part by typing the Digikey part number into google. There will be a link to the datasheet.

### Using the 3D Package Generator

Fusion360, being a 3D CAD modeling software, comes with the ability to create 3D packages illustrating your components. It also comes with a tool that will generate both 3D packages and footprints of your desired component, although you will need to edit these auto-generated footprints to meet class standards. In order to access this tool, create a new 3D package using the menu:

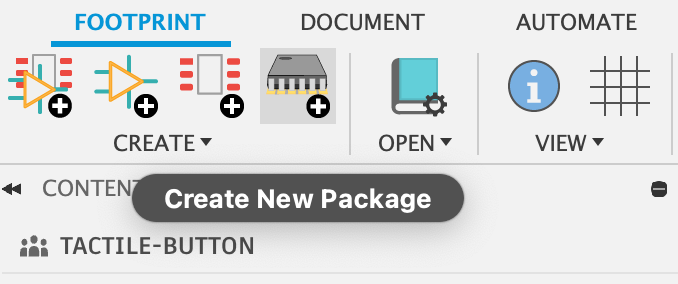
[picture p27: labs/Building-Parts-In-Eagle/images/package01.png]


If the 3D package generator menu doesn't show up in your newly-opened editor, you can open it using the menu option:

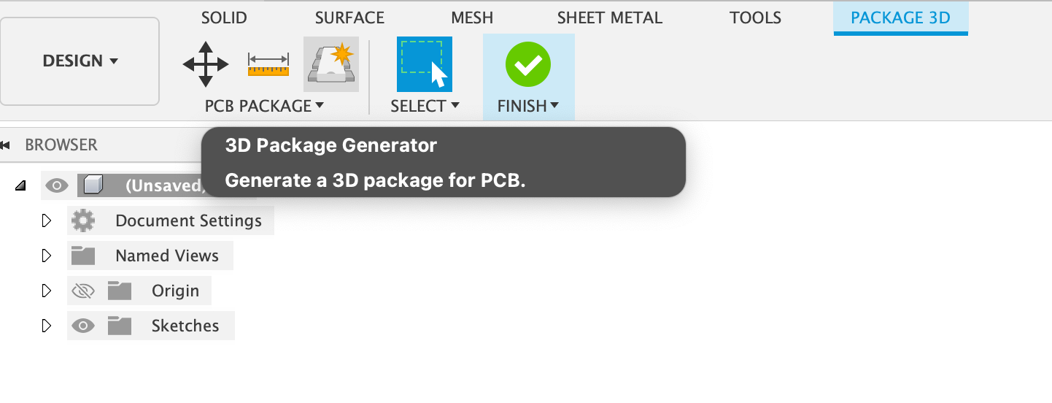
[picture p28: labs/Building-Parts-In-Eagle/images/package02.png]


A window will appear on your right:

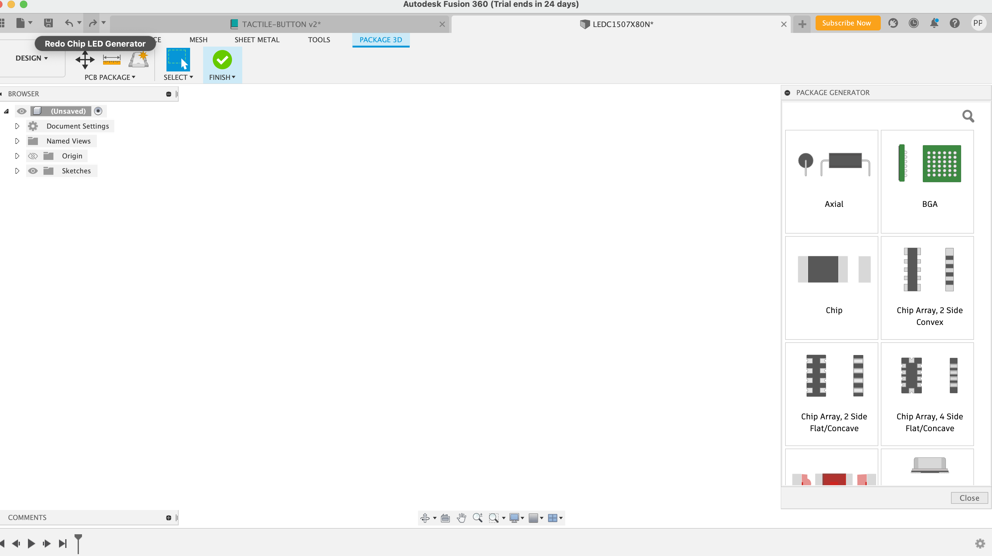
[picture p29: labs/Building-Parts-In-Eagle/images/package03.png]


After you select your desired part model from the list of options, you can input the dimensions from the datasheet. **Select "Nominal" for "Map silkscreen body"**:

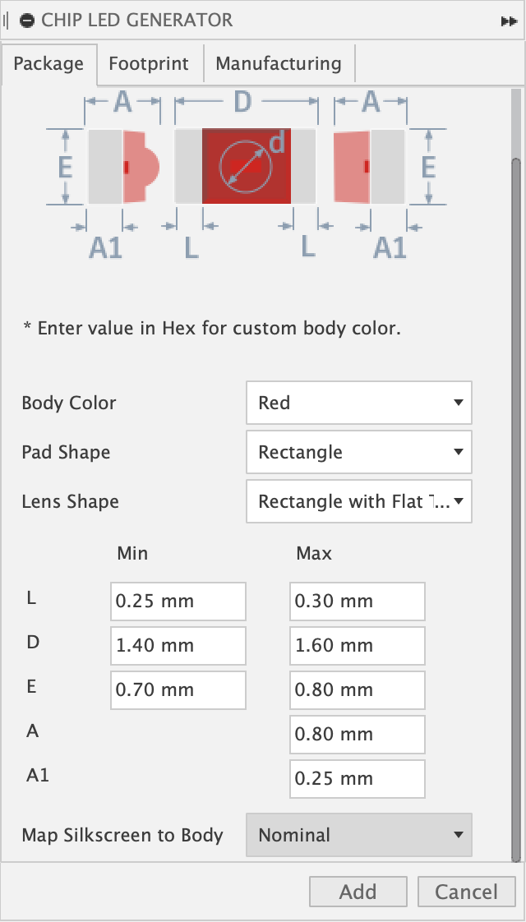
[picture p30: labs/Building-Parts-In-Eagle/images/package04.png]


Then your 3D model will appear! Click Finish at the top menu to close the 3D package editor and generate your footprint.

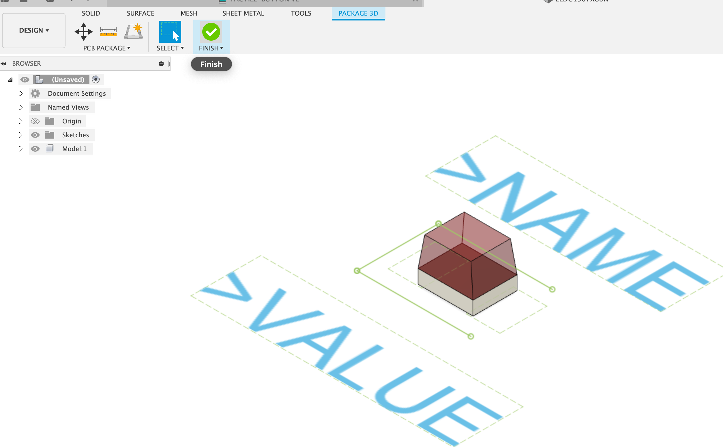
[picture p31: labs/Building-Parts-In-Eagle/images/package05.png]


Your new footprint will now appear within your library's list of parts. **Again, make sure to double check this footprint for adherence to this class's style guide, you will get warnings/errors if you don't.**

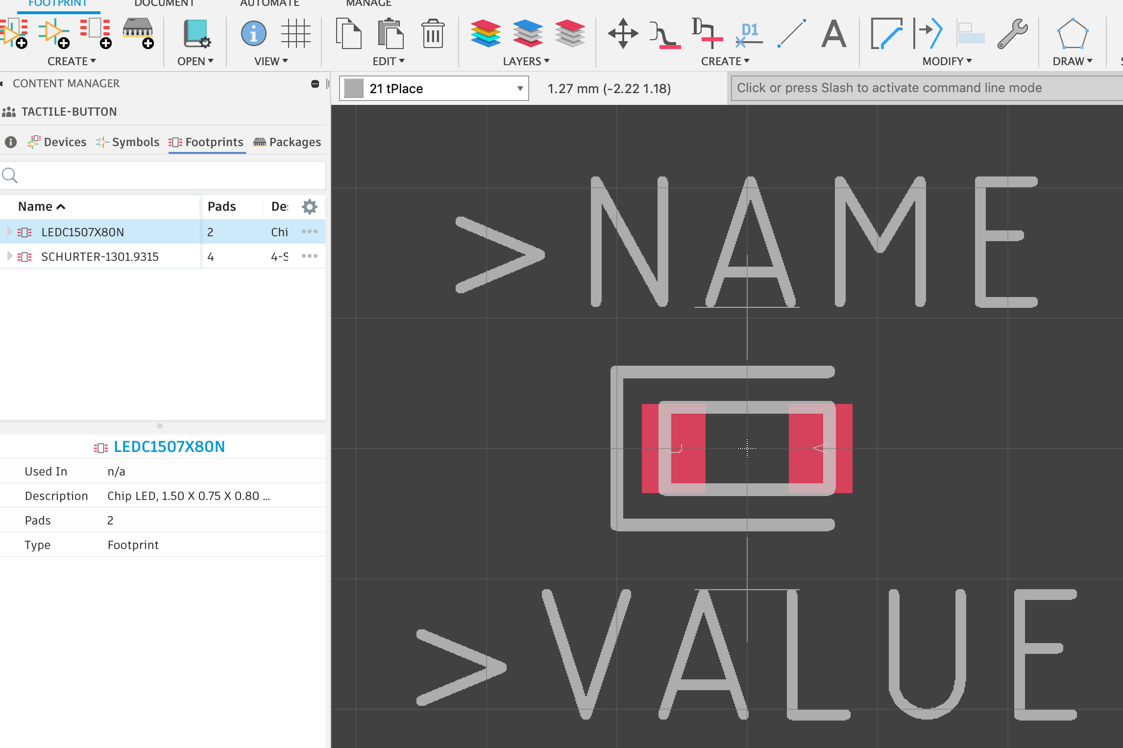
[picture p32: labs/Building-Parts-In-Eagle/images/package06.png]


For more information, check out [this Autodesk tutorial](https://www.youtube.com/watch?v=LlhIeRFX-N4&list=PLmA_xUT-8UlKE-U-eEqrkNEI7rd1fUnLY&index=4) for an example of how to use the tool.

### Guidelines for Building **Schematic Symbols**

When you design symbols follow these guidelines:

1. Choose a sensible name for the symbol. “Resistor” is a good name for your resistor symbol, since it can be used across all kinds of resistors. “CPU” is a bad name for the symbol for our microcontroller, since the symbol will be very specific to this particular chip, so the symbol name should reflect that.
2. For polarized parts include markings that make the polarization clear.
3. Make certain that your pins are placed with 0.1” grid settings. Failure to do so will cause you no end of pain.
4. For an IC (on anything with simple, rectangular symbol) Almost all your pins should go on the sides. The only exceptions are power pins (which can go on top), and ground pins (which can go on the bottom). Generally, inputs should go on the left and outputs on the right (this is not always easy to follow, but try).
5. Use standard symbols for components like resistors, capacitors, etc. Here are some examples: https://goo.gl/enZ0v0. You can also just google for “resistor schematic symbol” etc.
6. For two terminal, polarized devices, draw the positive terminal on the left (so it matches the footprints, see below).
7. For parts with many pins (e.g., the IMU and the microcontroller) arrange the pins on the schematic symbol thoughtfully. For instance, power and ground on the bottom or top (although they can go on the sides as well, probably near each other and probably with power above ground), and logically related pins near one another. In general it is not a good idea to mimic the physical arrangement of pins on the physical device: The physical arrangement of the pins based on engineering decisions. Your schematic symbol is about creating an easy-to-read schematic. I’ll reject designs for the IMU schematic symbol that just mimic the layout of the IMU pins.
8. Use sensible pin names that will help you connect the symbol pins and footprint pins correctly. For example, ‘1’ and ‘2’ makes sense for a resistor symbol, but “C” and “A” makes more sense for a diode. For parts with many pins (like the IMU) use names from the datasheet. The goal is to make it as easy as possible to check that you have connected things properly.
9. Sizes the symbols sensibly. Discrete components (e.g., resistors and capacitors) should be small, so they don’t take up too much space. Complex parts should be bigger to make them easy to wire up. For instance, the standard resistor symbol is 0.4x0.2 inches.
10. Include text elements with “>NAME” and “>VALUE” in layers “Names” and “Values” respectively, to show details about the parts. Only include “>VALUE” if the symbol will be used in devices that need a value (see notes below).

For the IMU, take a look at the microcontroller symbol for inspiration. It's in `quadparts_prebuilt.lbr`. It's laid out pretty nicely. It's more complex than the IMU and has more documentation on it than the IMU needs.

### Guidelines for Building **Footprints**

Each of your footprints should contain the following elements:

1. Choose a meaningful name: e.g, "0805_RESISTOR" or "0805_LED". Using the part number your are building for makes sense if there’s only one part that is that size, but for things like resistors, there are many parts (with different colors, resistances, etc.) that are the same size and you can reuse the footprint. Therefore, a name that reflects the type of footprint the part uses is appropriate (e.g., `0805_RESISTOR` is descriptive in this way).
2. Draw a box in tDocu that matches the nominal dimensions of the part. For parts with leads that extend from the part’s footprint (e.g., the MOSFET), you can draw in the leads too, if you want. tDocu doesn’t show up on the board.
3. Include a text item that displays the reference designator for the part. It should be on layer `tName` and the magic string “>NAME” is replaced with the reference designator.
4. Include a text item that displays the value of the part. It should be on layer tValues/ValuesTop. “>VALUE” is replaced with the value. This will show up in your assembly drawing to help ensure you install the right part.
5. Drawing elements on `tKeepout/ComponentExcludeTop` showing the area in which other part are not allowed. This should include the physical extent of the device and other other areas that need to be kept clear. See the note below about how to structure your `tKeepout/ComponentExcludeTop` lines.
6. The text for the reference designator (which appears as '>NAME' in layer `tNames/NamesTop`) footprint name should be in the “vector” font and of size 0.9mm with a “ratio” of 8. This is not the default for text in the footprint editor (if you figure how to make it the default, let me know). These settings make the reference designators as small as possible while still be legible.
7. The text for the reference designator should not overlap with each other or the silkscreen for the device.
8. The text for the reference designator should be aligned to 0.1mm grid (using a 0.5mm grid is better but not always possible).
9. You should tnclude text with “>VALUE” in the the `tValues/ValuesTop` layer if the part has a value (e.g., resistors and capacitors). Real-world designs don’t usually do this, but it makes hand assembly easier. ALl the boards for the class have values on the board. They should use the same font as the the reference designators (">NAME").
10. Add lines on `tPlace/SilkscreenTop` that guide the orientation, placement, and alignment of the parts. There are many different styles to consider. Google for “Resistor silkscreen” etc. for inspiration. Follow these guidelines:
    1. For polarized components, draw with the positive terminal on the left.
    2. For polarized components, make the positive terminal the first terminal.
    4. For polarized components, clearly mark the distinguished terminal with a dot or extra line. The distinguished terminal is the one that is marked in some way on the actual device, so you can oriente the mark on the device with mark on the board.
    5. For polarized componenst, make sure that the polarity marking will be visible when the part is installed (i.e., it should not be under the body of the part).
    6. When it makes sense, use familiar symbols to represent polarity (e.g., for a diode, you could use an triangle pointed toward the cathode). Design your footprint so that at least one polarity marker is visible when the part is installed (i.e. make sure all the polarity markers are not covered by the part.)
11. Make sure that the “>NAME” doesn’t overlap with the elements that show the orientation, placement, and alignment of the parts.
12. Make sure pads and SMDs are of uniform size, unless there’s an good reason not to.
13. Make sure pads and SMDs are aligned vertically and horizontally in rows and columns as makes sense for the footprint.
14. We may be soldering by hand, so you need to make sure the SMDs extend out from under the part. The SMDs should extend 0.5mm away from the edge of the footprint, except for the IMU.
15. Include lines or symbols in `tPlace/SilkscreenTop` to guide placement of the part. For parts like the IMU and MCU, this should make easy to precisely place the part by showing the correct, precise location of all four corners. For other parts an outine (or partial outline is sufficient).
16. Fusion360 includes a package generator (access it via the "new" button in the device window and select "Create with package generator"). You are welcome to use it, but the footprint it generates do not meet all of our requirements. You'll need to edit them a bit.

#### The Courtyard and tKeepout/ComponentExcludeTop

One of the goals of a good library is to make it easy to make sure your board looks good, is easy to assemble, and easy to verify. Part placement is a key part of all three, and the "courtyard" is the key to guiding how you place parts. The courtyard defines the area of the PCB that the part occupies. This includes the part physically and it's pads, but also include some extra space that makes it possible to place the part on the board. The size of the courtyard depends on how the board will be assembled. In our case, it's by hand, so we need a pretty big courtyard. I should suggest having the courtyard extend at least 1mm beyond the boundary of the part and its pads.

Fusion360 use `tKeepout/ComponentExcludeTop` to describe the courtyard. The rule is that if `tKeepout/ComponentExcludeTop` for different parts overlap, it is an error that will be flagged during DRC. Unfortunately, this means that if you draw your courtyard on a consistent grid (which you should), then when two parts are perfectly placed next to eachother, the `tKeepout/ComponentExcludeTop` defining their courtyards will overlap. There are two bad options: move the parts farther apart (which takes up space) or tolerate the DRC error (which will increase the possibility that you ignore real errors).

The third, preferable, option is to draw your courtyard on 0.5mm grid and then 'inset' them by 0.1mm. This will let you place parts close together without generating suprious DRC errors. The resulting board layouts are very tidy.

The width of your `tKeepout/ComponentExcludeTop` lines should be 0.05mm.

Note that the courtyard should not surround the `>NAME` and `>VALUE`. Two reasons:

1.  You'll probably end up moving the reference designators around (which you can do freely on the board layout)
2.  You'll have to pack parts together more closely than such a large courtyard will allow. The result will be that you'll ignore a bunch of DRC errors and end up having to manually enforce reasonable spacing between parts.

### Guidelines for Building Devices

Devices connect footprints to schematic symbols and provide information necessary to purchase and install an eletronic component.

Follow these guidelines when creating devices:

1. The device should have a generic name, if it will have many variants. For instance, a “Resistor” or “Capacitor” device will have variants for different footprint sizes and values.
2. Put the symbol at the origin (in the left-hand pane of the device editing window)
3. Choose a sensible name for the device. The guidelines for symbols generally apply here as well.
4. When you create variants in the device, give them descriptive names. For instance, for 10Ohm, 0805 resistor, “-100R-0805” would be good name. Avoid having an unnamed variant unless there is really only ever going to be one variant.
5. Be selective about what information you put in the variant name. The size, value (resistance, capacitance, color, etc.), is a good idea. You should only include information that will be useful to you when selecting which variant to use.
6. Make sure to connect the symbol pins to footprint pins correctly. Check it, check it again, have your partner check it. This is a common source of hard-to-find bugs.
7. Set the “Value” radio button appropriately. Things like resistors and capacitors naturally have a value (i.e., a resistance or a capacitance), others, like the microcontroller, do not. If you set the value radio button, your schematic symbol should include ">VALUE" in layer `Values`.
8. Set the prefix appropriately: “R” for resistor, “Q” for mosfets, “U” for ICs, “D” for diodes, etc. This is what Fusion360 will start the reference designator with (e.g., “R1”, “Q2”).

You should have one variant for each different physical device you might include in your design. For instance, if you have two 0805 resistors with different resistances, you should one variant for each of them. In this case, you should add an attribute (see below) called “VALUE” that specifies the value (e.g., “10R” for 10 Ohms, “1nF” for 1 nanofarad).

You can attach metadata to each variant of your device using "attributes." (Fusion360 provides the notion of "technologies" which are different sets of attributes for a device. You should always use the unnamed technology: "") All your variants should have the following attributes:

- `DIST` – distributer (For us, this is always “Digikey”)
- `DISTPN` – Distributer part number. i.e., Digikey’s part number. This is different from the manufacturer’s part number.
- `CREATOR` – Your name, if you designed the part.

All these attributes should be “constant” which means you can’t change them on a per-part basis in the schematic. Set this via the drop down in the attribute editor window.

`DIST` and `DISTPN` are especially critical, because when we go to order parts for your quadcopter, we will use this information to know what to order.

### Notes on Individual Parts

The data sheets for all the parts are in `QuadClass-Resources/Datasheets`.

#### Resistor

- Include “RES” in the name of the device you create, so Eaglint can find it.
- Check the `resistor_mounting_PYu-R_Mount_10.pdf` for guidance about the footprint, but...
- Make sure SMDs extend 0.5 mm beyond the end of the resistor.
- The prefix for your resistor device should be “R” for resistor.
- Name the variant so it’s clear it’s a 0 Ohm resistor. Something like “-0Ohm” or "-0805-OOhm" would make sense.

#### LEDs

- When generating the 3D package, choose "Chip LED" as your model.
- Include “LED” in the name of the device you create (so Eaglint can find them).
- The prefix for your LED device should be “D” for diode.
- Positive terminal on the left on both symbol and footprint.
- Name the cathode ‘C’ and the anode ‘A’ on both the symbol and the footprint.
- Make sure SMDs extend 0.5 mm beyond the end of the LED.
- Name the variant so it’s clear it’s a red LED (it is a red LED because it has the DISTPN that corresponds to a red LED)
- In your footprint, mark the SMD that connects to 'distinguished' pin of the physical device (see below).

Any physical part for which orientation (or polarity) is important will have some marking on it that distinguishes one terminal from the others. On the IMU or the microcontroller or the IMU, this is a dot near pin 1. For tiny devices like LEDs, it'll be some kind of mark. For this LED it is two green rectangle drawn on the top of the LED under the plastic 'lens' that forms the top of the LED. You can see them drawn on the mechanical drawing in the data sheet.

Your footprint should include some kind of marking that marks the SMD that should attach to the distinguished pin. Is the distinguished pin the cathode or the anode?

#### MOSFET

- When generating the 3D package, choose "SOTFL" or "SOT23" as the model.
- Include “FET” in the name of the device you create.
- The prefix for your MOSFET device should be “Q” (that’s the conventional prefix for transistors).
- Since we are using an NMOSFET (as opposed to a PMOSFET), current flows from the drain to source, so put the drain on top in the symbol.
- Name the source, drain, and gate, “S”, “D”, and “G”, respectively in both the symbol and the footprint.
- Read the section in the datasheet about SMD layout starting on page 6 (make sure your looking at the datasheet provided in the "Resources" git repo. The datasheet online is missing this page).
  - There are two aspects of SMD sizing you must address in this footprint. The first is the size of the metal SMD. The second is the hole in the solder mask, called the “stop mask” because it stops the solder mask. Normally, SMDs come with appropriate ‘stop’ by default. You’ll need to remove the default stop and add yours by hand.
  - Create the SMDs according to the guidance in the datasheet.
  - Use the info tool to edit each SMD, and uncheck ‘stop’.
  - Draw in the stop by hand in layer `tStop/SolderMaskTop` with the rectangle tool. The geometry of these rectangles should correspond to the “recommended minimum pads” in the datasheet.
  - You will need to draw in rectangle on `tCream/StencilTop` as well (and disable the "Cream" check box in properties dialog). Your `tCream/StencilTop` can (and should) be identical to your `tStop/SolderMaskTop`. `tCream/StencilTop` specifies where solder paste will be applied during assembly.

#### IMU

The IMU has caused us significant problems in the past. Be careful with it. You should read both the datasheet and the SMD tech note (look for `IMU_*` in `QuadClass-Resources/Datasheets`).

- There should be no metal under the IMU. To enforce this, you should do the following
  1.  Draw a rectangle (using the rectangle tool, not four lines in a rectangle) in `tRestrict/RestrictTop` that fills most of the space in under the footprint, but does not overlap any of the pins.
  2.  Draw a rectangle (using the rectangle tool, not four lines in a rectangle) in `bRestrict/RestrictBottom` that covers the entire footprint.
  3.  Draw a rectangle (using the rectangle tool, not four lines in a rectangle) in `vRestrict/RestrictVias` that covers the entire footprint.
  4.  You have to use the rectangle tool, because lines will only eliminate the line, not the interior.
   In the symbol for the IMU, make sure that all the pin names are visible (i.e., not overlapping and with some some space between them).
- ~~There should be no solder mask under the middle of IMU. To enforce this, draw a rectangle of `tStop/SolderMaskTop` that covers the area under the footprint, but does not overlap the pins.~~
- Include “IMU” in the name of the device you create.
- You should compute the SMD width based on the IMU datasheet and the `Datasheets/IMU_Soldering\ guidance-{1,2}.pdf` documents. You will need to read them quite carefully.
- The prefix for your IMU device should be “U” (that’s the conventional prefix for ICs).
- Label the SMDs on the IMU using either the pin numbers or the names used in the datasheet. Some pads same replicated names. Use something like “GND1”, “GND2”, etc. to distinguish them.
- Be sure to include a pin-1 indicator that will be visible when the IMU is installed.
- There are a bunch notes in the technical notes about soldering guidance that say to not solder the pin-1 indicator. Our IMU does not have the kind of pin-1 indicator they are referring to, so that guidance does not apply.
- ~~You will note that it appears that there will be no solder mask between the pads because the `tStop/SolderMaskTop` for the pads overlap. The width of the automatically added `tStop/SolderMaskTop` is controlled by the `.dru` file we use during board layout and our DRU file will ensure that solder mask remains. However, the DRU file doesn't affect how the `tStop/SolderMaskTop` appears in the footprint editor.~~

## Turn in Your Work

### Commit the following:

1. Your `lbr/custom.lbr`
2. Submit it though Eaglint: http://eaglint.nvsl.io.

### Rubric

“Perfect” score: 10

Initial points: 12

You will lose 0.5 points for failed full design check or human review and 1 point for each day late.

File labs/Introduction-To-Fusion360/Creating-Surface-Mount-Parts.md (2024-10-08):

# Part 4: Creating Surface Mount Components

The design we have so far for the flashlight uses "through hole" parts. This means that the pins for the part protrude through the board and are soldered into place by filling the hole with solder. Through hole parts are easy to work with, but they are bulky. Also drilling so many holes through the board makes it harder to route more complex boards since the holes occupy space on all the layers of the board (front, back, and any internal wiring layers).

Most modern PCBs use "surface mount" (also called SMD) parts that are more compact and only require connections to one side of the board. They are also harder to solder. Many of the components we will use are only available as surface mount, and many components are available as both surface mount and through hole.

The course style guidelines for libraries are in the "Guidelines for Building..." section of [this lab](https://github.com/NVSL/QuadClass-Resources/blob/master/labs/Building-Parts-In-Eagle/README.md). Read and follow them. Eaglint will complain if you don't.

## Preparation

Create a new schematic and board files named `smd.sch` and `smd.brd` and load the DRU file for error checking. Remember for creating a new design `File->New Electronics Design` and save the design as `smd`. Then in the design tab `Create->New Schematic` and save the schematic as `smd`. Then in the design tab `Create->New Board` or in the schematic tab `Switch to PCB document`. Add the same components, with the exception of the through-hole push button. You can add the components into the schematic manually. However, if you are a desperate person as me, instead of adding the components again manually you can copy the entire schematic by going to the throughhole schematic tab, then clicking `Group Select` and selecting all components including the FRAME, then Ctr+C, then switch to the smd.sch tab and Ctr+V. Finally, delete the through hole push button. The tabs and smd schematic should look as follows:

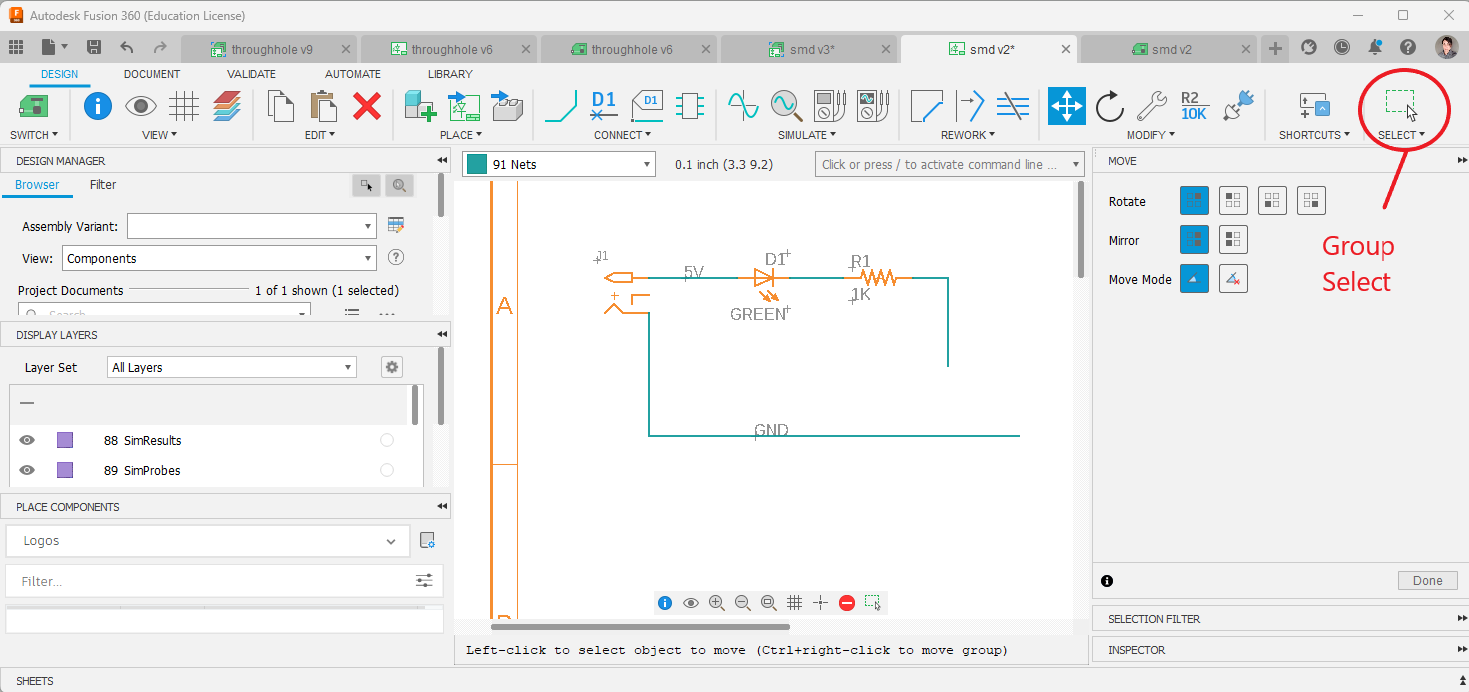
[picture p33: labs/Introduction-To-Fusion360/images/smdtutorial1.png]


This time instead of adding the throughhole (TH) push button component from a library we will create our own push button component inside a library which will be surface mount (SMD) instead. We will create part number [1301.9315](https://www.digikey.com/en/products/detail/schurter-inc/1301-9315/2643952) which has the following [datasheet](https://www.schurter.com/en/datasheet/typ_6x6_mm_tact_switches.pdf). It's the one that looks like this:

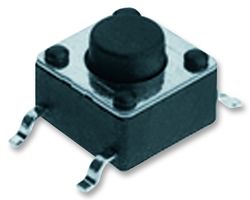
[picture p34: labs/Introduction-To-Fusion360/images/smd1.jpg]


In datasheets is common that manufacturers show many dimensions for different versions for the same family of components. Also, they show two types of dimensions, the physical component dimensions and the PCB pads recommended dimensions. We will use the dimensions **of the recommended PCB pads** which in the datasheet correspond to the `LSH Gullwing lead` version:



If you can't access the datasheet for the SMD push button please ask the TA.

## Creating a Surface Mount Component

All electronic components are stored inside libraries (\*.lbr files), and include schematic symbols, PCB footprints, and 3D packages. Now, Adafruit has a very nice [tutorial about building new schematic symbols, packages, and devices in Eagle](https://www.google.com/url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). However, since this tutorial's release, Eagle has been ported over to Fusion360. Autodesk has released several tutorials on how to design custom parts, which can be found [here (~15 min)](https://www.youtube.com/watch?v=zqar0XWtFaY) and [here (~45 min)](https://www.youtube.com/watch?v=xNIEXCimRSg&list=PLmA_xUT-8UlKE-U-eEqrkNEI7rd1fUnLY).

We will go step by step creating the SMD push button component. However, it's recommended that you go through any of the above tutorials for further reference. We recommend the more recent ones from Autodesk.

Go to your Github repo folder and make a copy of `Lab01.lbr` called `Lab01_smd.lbr`, we will create the SMD push button there.

Open `Lab01_smd.lbr` in Fusion360. `File->Open...->Open from my computer->Lab01_smd.lbr`, you should be able to see the following tab:



## Create a new Footprint

The footprint refers to the PCB pads (exposed cooper) where the SMD push button legs will be soldered into the PCB. Click `Create New Footprint` and give it the name of `SCHURTER-1301.9315`.



Change the Grid to `0.25 mm`. For footprints, it's recommended to use the grid that makes sense to follow the dimensions for the SMD push button pads shown in the datasheet.



Now it's time to add the SMD button pads. Click `SMD pad` and place the pad in X,Y position `[-5.00 -2.25]`. On the top center you can see the position of your cursor with the pad. By default, for placing pads the center of the pad is taken as reference.



Why that position? Remember, we are trying to recreate the same pads with the same dimensions shown in the SMD push button datasheet. So if the pads require a Y spacing of 10.00 mm, 10.00/2 is 5.00 mm. Same for X spacing, 4.5/2 equals 2.25 mm. **Taking as reference the center**, the first pad (down left) should be placed at -5.00 mm, 2.25 mm. That will give us the correct dimensions. That's also why we set the grid to be 0.25 mm, so we can have a precision of 0.25 mm.

Add 3 more pads in the X,Y positions: `[5.00, -2.25]`, `[-5.00, 2.25]`, `[5.00, 2.25]`. The final result should look like this:



We are missing the pads dimensions which, taking as reference the datasheet, are `2.10 mm X 1.40 mm` for each pad. Use the Info button to correct the size for each pad.



All pads need to have a number, which is used to know the orientation of the component and to make the right connections within the component. Use the numbering reference in the datasheet to number the pads (the image below the pads dimensions).

⚠️ I'm serious! Pay attention to the numbering. If you number the pads wrong it can make you, for example, connect pads 1 with 3 and 2 with 4, which is a short (push button always pressed). This error has happened to me before for not paying attention, and you can only figure the error out after the board has been assembled.



Now it's time to add some silkscreen information. Silkscreen information are the white lines and text on top of the green soldermask. Can you omit the silkscreen information? Yes, but if you are soldering each component manually, as we will do, you will need to go through the PCB design component by component and figure out the values, names, and orientation of each component. Adding a visual reference in the PCB makes placement much easier, also make your board more repairable making others understand more about your design.

There are three types of silkscreen information: Names, Values, and Placement & Orientation information. In Fusion 360 these layers are reserved as tNames/NamesTop & bNames, tValues/ValuesTop & tValues/ValuesTop, and tPlace/SilkscreenTop & bPlace/SilkscreenBottom, where "t" stands for "Top of PCB" and "b" stands for "Bottom of PCB". Our design will place all components on top, so we only need to add information on the top. If you move components to the bottom in your PCB, Fusion 360 automatically switches the silkscreen layers.

Now it's time to add placement information on the `tPlace/SilkscreenTop` layer. We will draw a 2D representation of the push button to let us know that a push button goes there. Change to layer tPlace/SilkscreenTop, and then draw a square in the middle of the pads that represented the case of the push button, it should look as follows:



Now draw a circle representing the push button. Choose Circle from the Draw drop down menu to draw the push button button. There's no need to be precise with the drawing, the only thing that matters is that you make it understandable that a button goes there between those pads.



It's also important in some components to indicate which one of all those pads is the first pin, that way we know the orientation the component should be placed. For push buttons, it's not necessary since the push button can work in either orientation, however in the case of a microcontroller, if you don't place a microcontroller chip in the right orientation your circuit won't work. Although orientation information is not necessary for push buttons, let's indicate which pad is the first pin by drawing a small circle next to the first pad. After drawing the circle click on information and select the circle you just draw to view its properties. Increase the width of the circle and make it look like it's filled.



Let's move now with name information. tName should contain the [reference designator](https://en.wikipedia.org/wiki/Reference_designator) of the component (e.g., R1, R2, C1, S1, etc). We don't know this information yet, however Fusion360 has an annotation format that works as a placeholder. Change to layer `tName`, then click the "A" (text) button and enter `>Name`. With this we will indicate Fusion360 that that value should be replaced by the reference designator assigned automatically when you include the part into the schematic.



Change the text to be at least `0.9 mm` high, have a `weight of 8%` and be in the `“vector” font`. Otherwise, the manufacturer company can have problems printing such small text. Use the information button to make that change to ">Name". Note that first you need to change from proportional to vector and click apply, then adjust the other values. Finally, center the text.



Value information contains information such as the resistor and capacitor values (e.g., 1k, 22K, 0.1uF, 10ufF) or the manufacturer's part number (e.g, 1301.9315, ATMEL128RF). Follow the same steps as >Name, but now for `>Value` using the `tValue` layer. Note that you can change the text properties directly or by clicking the info button. The result should look like this:



Finally, change to the `tKeepout/ComponentExcludeTop` layer and draw a box around the component using the line button. Make sure the lines start and end in the same coordinates. This Keepout layer is not common in designs, and it's not necessary when you know what you are doing, however it's useful for preventing you from placing components too close to each other. Also, by making this tkeepout box bigger or smaller you can indicate, for example, that you need extra space for manually soldering a particular component, and that you don't want other components close.



For more info about how to create a footprint in Fusion360 check out [this video](https://www.youtube.com/watch?v=8-tJZHFzWXo&list=PLmA_xUT-8UlKE-U-eEqrkNEI7rd1fUnLY&index=3).

## Create a new Symbol

Now let's make a schematic symbol for the SMD push button component. Schematic symbols provide an easier visual representation of components, instead of using irregular footprint shapes. The schematic symbol can be as simple box with pins, however you make easier for people to interpret your schematic if you use the [standard schematic symbols](https://en.wikipedia.org/wiki/Electronic_symbol). Note that in industry, not everyone follows the standard, drawing symbols can consume precious time and some people just draw boxes, however others like to challenge the standard and draw some fancy symbols' art, just be aware of this. For this tutorial let's try to follow the standard schematic symbol for push buttons.



Create a new symbol and call it `TACTILE-BUTTON`.



Add two pins of medium length. The pins are the most important part of the symbol. Is where the schematic lines will connect to. The rest is just drawing for better visual understanding. The pins should match the pads in the footprint, however we will only draw 2 and later we will see how to assign multiple pads to one schematic symbol pin. Note that you can change the pins directions to be of type pwr (power), out, in, etc. Changing the pins direction makes sure you make the right connections. However, for now "io" (input/output) direction is fine, also if you are not sure, always use "io" direction.

⚠️ Note that it's very important not to change the grid when placing pins, keep it as `0.1 inches`, otherwise when you add the symbol into the schematic which has a different grid it will be hard to make pin connections.



Now, name the pins as `A` and `B`, use the naming tool for this. While footprints naming convention usually use numbers (1, 2, 3, 4....) which makes it easier to know the position and orientation, for the symbols you should name the pins with a name that represents what the pin will be used for (e.g., GND, 5V, EN, SDA, SCL). Push button pins doesn't have any extra capability, like providing power, etc and are simple connections, so that's why we name the pins simply A and B.



In most cases we want these pin names to be visually shown (e.g., GND, 5V, EN, SDA, SCL), however in the case of push buttons, since it doesn't matter how you connect the push button in the schematic, we can turn off the visibility of the pin names. Change the visibility to only pad, this means that when you make a connection, only the pad number will be shown.



Draw the push button symbol using lines and circles. Instead of changing the grid for drawing you can use "ALT" and move the lines and circles into coordinates different from the grid. Your design should look something like this:



Schematic symbols also need name and value information, Use `95 Names` layer to add the text `>Name`, and `96 Values` layer to add the text `>Values`. For symbols, you don't need to change the text to vector since we are not going to print this information into the PCB, keep the text as proportional.





## Create a new Component

Finally, it's time to create a component which consist of a footprint and a symbol.

Create a new component and call it `TACTILE-BUTTON`.



Click on `add symbol` to add the symbol you just created.



⚠️ It is important that you align the origin/center of the symbol with the origin/center of the workspace area.  
You should end with the following:



Click `New->Add local package` to add the footprint you just created.



You should end with the following:



Now, what we have waited all the time, it's time to link symbol pins with footprint pads. Be very careful with this process, if you make wrong pins-to-pads link your connections won't match, and you will be wondering why a 5V pin was connected to a GND pad. Select the text with a warning symbol and click `Connect`, a window as the following should show up.



Now connect `pin A with pads 1 & 2` and `pin B with pads 3 & 4`. Use "ALT" to select multiple pads and then click connect.



You should end with the connections as follows:



Click "OK" to accept the connections. You should now see a green check mark for the connections.



Add the reference designator prefix for that symbol (e.g, R, S, C). Use this link to search for the [reference designator](https://en.wikipedia.org/wiki/Reference_designator) for switches, and locate where it says switch.



Add the `"S" prefix` by clicking the prefix button.



Make the footprint a variant and name it `-SCHURTER-1301.9315`. Variants are helpful so that you don't need to redraw the symbol. You can make a different footprint, maybe bigger push button and add to it the same schematic symbol using a variant. Right-click on the footprint text and select "Rename", you should now be able to rename to pad-to-footprint connection.

⚠️ All variant names should start with a dash, for example -\<varian name\>.



We now have a working component, however there's one last step, and that is of giving the component additional information. Like whom created it, who's the distributor, what's the manufacturer part number for this component, etc. You can find most of the useful information from the distributor, in this case [Digikey](https://www.digikey.com/en/products/detail/schurter-inc/1301-9315/2643952). Note that there are many other components distributors (e.g. [Mouser](https://www.mouser.com/), [Arrow](https://www.arrow.com/), etc).

Adding attributes also makes it easier to automatically generate the list of components you need to purchase.

Add three "attributes" to the new variant you created, which can be added using the `Attribute` button:

- "CREATOR" This should be your name, since you created the variant.
- "DIST" for distributer. This is where we buy the part from. Put "Digikey"
- "DISTPN" for distributor part number. Put "1301.9315".



These attributes should be of type `constant` instead of variable.



Congratulations! 🎉 You have a working SMD push button component.



Save your component (Ctr+S).

## Adding the SMD push button component to your schematic

Go to the `smd.sch` schematic, select add new component, and select the library `Lab01_smd` which has a teams symbol.



You will see that the library is there, but your new component may not be there. What's happening? What's happening is that the library version that the schematic sees has not been updated. To update the library with your changes click `Update design from all libraries used in design`



Now add your SMD push button and complete the schematic.



You will notice a strange text in the assigned value text for the symbol. That's a text composed of the component name plus the variant name. This text is not necessary for push buttons, so we can go to the component library and turn the value `"on"` (Don't ask me why on when it should be off).



Go to `smd.sch` and update all libraries again.



We now see the text below is gone, and this gives us opportunity to add any value. This is useful for assigning values to resistors (e.g, 1K, 370 Ohms).



Bonus: If you want to give your component a fixed value, add the attribute "VALUE" and "\<Your FIXED VALUE\>".

## Completing the Board

Change the board grid to `0.5 mm`. Add the DRU file `jlcpcb-2layer.dru` going to "RULES DRC/EC -> DRC -> Load ...". Move the components into the board, adjust the board outline and finally set the outlines' width to `0.01mm`.



Now, re-route the board, but now using the `Autorouter` tool. The autorouter tool will trace everything for you. Keep in mind that the autorouter tool is very inefficient, you will sometimes need to add more layers or more board area for the autorouter to completely trace your design. For the most efficient design route your board manually.



Click continue.



Click start



The process will create multiple threads that will execute path finding algorithms. When it's finish click End Job.



This will result in a nice, fully-routed board!



You can select “Unroute -> Unroute all” to remove all traces and try again.

Check for any DRC errors: "RULES DRC/ERC (tab) -> DRC -> Check". If no window pop-ups with errors, it means your board doesn't have any errors.

## Re-running the CAM Processor

Follow the instructions for running the CAM processor given in the previous part. Make sure to use CAM file `Eagle/CAM/pcbcart-4layer.cam`. In the Gerber viewer, you can find the pads for the SMD push button the in the GTL layer. If you check the GBL layer, you’ll notice that while the pins for all the through hole parts appear on the bottom of the board, the pads for the surface mounted component does not. This gives more space to place more components and add more routing.

Save the Gerber file as `smd.cam.zip`.

Once you've done everything, you're ready for the [final steps](README.md#getting-art-onto-the-board): adding artwork and exporting!

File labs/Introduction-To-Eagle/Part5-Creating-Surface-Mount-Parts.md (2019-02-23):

# Part 4: Creating Surface Mount Components

The design we have so far for the flashlight uses "through hole" parts. This means that the pins for the part protrude through the board and are soldered into place by filling the hole with solder. Through hole parts are easy to work with, but they are bulky and drill so many holes through the board makes it harder to route more complex boards since the parts effectively occupy space on all the layers of the board (front, back, and any internal wiring layers).

Most modern PCBs use "surface mount" (also called SMD) parts that more compact and only require connections to one side of the board. They are also harder to solder. Many of the components we will use are only available as surface mount, and many components are available as both surface mount and through hole.

## 

## Creating a Surface Mount Device
We will replace the through hole button with a surface mount version. We will use part number 1301.9315 from this [datasheet](http://www.google.com/url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). It's the one that looks like this:

[image:https://lh3.googleusercontent.com/ipQKmcLF5KH0FEmhhh2LshnmnWO_S6q-gVyUcMGCm8SqTT_b8pg88bL5_yflfAWCrWgID45S=w271]

Adafruit has a very nice [tutorial about building new schematic symbols, packages, and devices in Eagle](https://www.google.com/url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). Go through the tutorial using this tactile button instead of the lux sensor they use in the tutorial. The datasheet required is present in your Lab 01 repository. Make a copy of `Lab01.lbr` called `Lab01_smd.lbr` and create the package there. Create a new package, device, and symbol for the button by following the ADAFRUIT tutorial. 

### 

### Reading Datasheets
Interpreting datasheets takes some practice. Here are some tips:

* The datasheet includes data on many switches. Make sure you are looking at the correct part of the sheet.
* There are several mechanical drawings. For creating a package, you are interested in solder pad layout.
* Don't assume drawings are for scale. Instead, use the numerical values given.
### 

### Additional Requirements for Your Package
The package should be called `SCHURTER-1301.9315`, the symbol should be called `TACTILE-BUTTON`, and the device should be called `TACTILE-BUTTON`, and the variant should be called `SHURTER-1301.9315`.

Name the pins to match the PCB layout drawing in the data sheet, and orient your package to match the drawing as well. This is a good practice because it makes it easy to see that your package matches the drawing.

Make sure that the length of your smds in the long dimension, and the width is the shorter dimension.

### 

### Additional Requirements for Your Symbol
Your symbol should have just two pins (whereas the symbol you used in your throughhole schematic had 4). They should be called `A` and `B`, and pressing the button should connect them electrically.

Note that your package has four SMDs. You'll need to connect two SMDs from the package to a single pin in symbol. You do this in the "Connect" dialog. Just select one pin and two pads, and click connect.

### 

### Additional Requirements for Your Device
There are a few other things you'll need to be sure of in the package you build:

* You need two add three "attributes" to the new variant you created

	* "DIST" for distributer. This is where we buy the part from. You can put "NA"
	* "DISTPN" for distributor part number. You can put "NA"
	* "CREATOR" This should be your name, since you created the variant.
	* You can add attributes by clicking on "attributes" in the device editor window:

[image:https://lh4.googleusercontent.com/RQN_yY4LOx5fnP-gO2C3XqTy9bbn9XhsK3nWCb8WqxxaqILB44G_hkMYicC3D94LWWNMsDI=w472]

		* You also need to be sure to draw a box around your package in layer ‘tKeepout’.
* You need to add a text item in layer “tName” that contains “>NAME”. This will be replaced with the parts name. To render clearly, the next needs to be at least 1.27 mm high, have a weight of 8% and be in the “vector” font. You can set these parameters in the tool bar at the top of the window or by using the “info” tool to change the attributes of the text after you create it.
## 

## Replacing the Through-hole Component
You can use your new SMD button just like our own through-hole button. Just delete the old button and replace it with your new button.

##
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

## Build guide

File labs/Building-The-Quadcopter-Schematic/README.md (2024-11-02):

# Assembling The Quadcopter Schematic

To be completed in pairs.

Check course schedule for the due dates.

## Skills to Learn

1. Design a schematic to match a written specification.
2. Integrate portions of a reference design into your schematic.
3. Read and understand key portions of part datasheets.

## Equipment, Supplies, and Software You Will Need

1. Create a team in eaglint. You _must_ do this before clicking the starter link below.
1. The repo you started in "Programming the Hardware Lab"
1. The `custom.lbr` library you built in previous lab, OR your cloud save for the custom library. From here on out, maintain copies of your libraries on the cloud.
1. Read through the [Fusion Tricks Page](../../Fusion-Tricks.md) and skim the [Autodesk docs](https://help.autodesk.com/view/fusion360/ENU/?guid=ECD-SCHEMATIC) that go over the design tools you will use this lab.

## Preliminaries

### Setting up Fusion360

The repo for this lab will evolve to hold all the hardware and software for your quadcopter for the remainder of the quarter.

Now would be a good time to start utilizing Fusion Teams. To get started, decide between you and your partner on whose `custom` library should be used. That person should locate the Team online manager in the Data panel on the left:

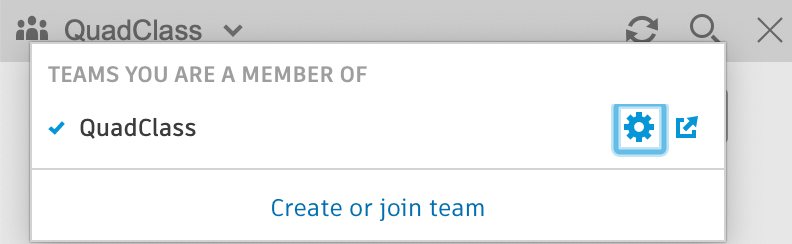
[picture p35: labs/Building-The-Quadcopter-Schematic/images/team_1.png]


This will open up a web browser to manage your team. You can edit the name, invite your partner using their email, and have shared access to a cloud version of your library! Rename it as `custom_<name>` so that the versions from both team members can co-exist. If you run into issues with one partner's library, you can always import your other library into Fusion360, just be sure to maintain them using the cloud! You should not reference local versions of `.lbr` files, and you should only export them when you are ready to submit.

To clean up local copies of previously-used `.lbr` files, and to remove unnecessary third-party libraries, you can remove them using the library manager (make sure to keep your team's library in use):

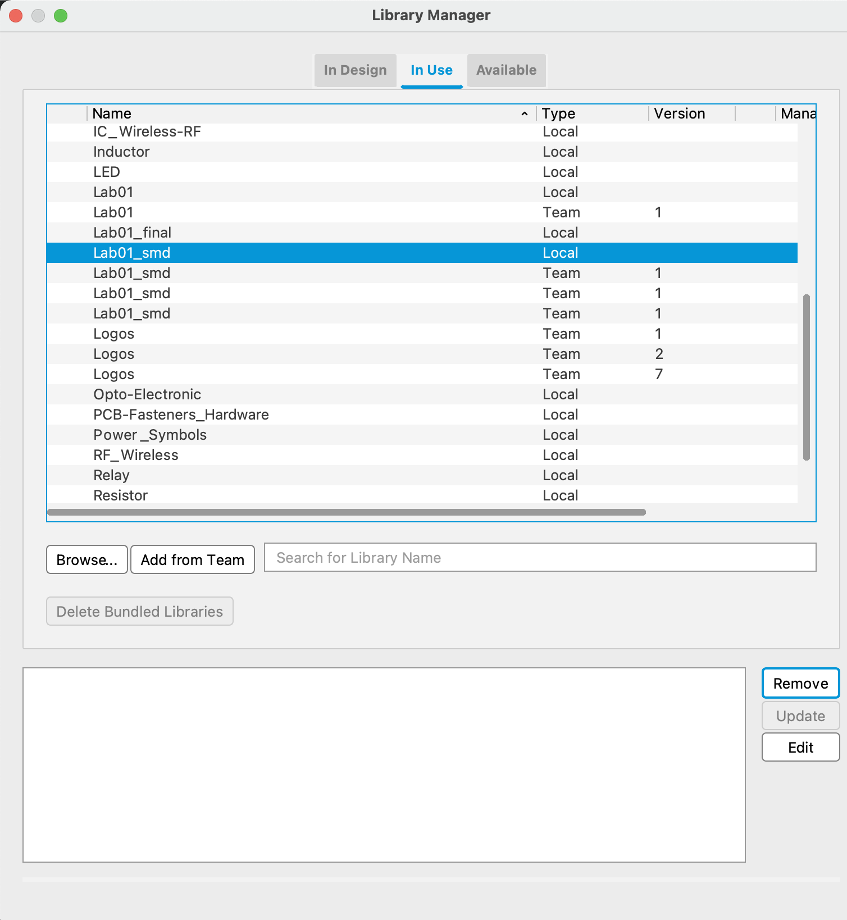
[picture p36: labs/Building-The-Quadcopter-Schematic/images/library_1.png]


Feel free to remove all libraries except for your `custom` team library from last lab.

### Dealing with GitHub and Fusion360

Both GitHub and Fusion360 provide a mechanism for you to collaborate with your partner on the design:

- Fusion360 requires you to keep all your design files in the cloud and it allows you to share your design with other members of your team. This means that you and you're partner will be working on the same files. This is reasonably convenient and deeply integrated into Fusion360.

- GitHub uses the clone/commit/push process you are familiar with.

These two mechanisms don't work especially well together, unfortunately. The main problem is that getting files in and out of Fusion360 so you can work with them in GitHub is a hassle during collaboration.

Here is what has worked reasonably well in the past:

1. Use Fusion360s collaboration mechanisms while working on your project. It saves intermediate versions, so you can always roll back.
2. Only export your work from Fusion360 and commit it to GitHub to run it through Eaglint and turn it in.

The last step is a still a bit of a pain, but Eaglint doesn't know how to communicate with Fusion360 (yet), so there's no other option.

### Make Fusion360 Easier to Use

By default, Fusion360 comes configured with a bunch of libraries that can make it hard to find the libraries we are using for this class. This is controlled by the directories Fusion360 is setup to look in for library and other files. You can change the directories by selecting `User->Preferences` (upper-right corner) and then selecting `General->Electronics->Directory`.

To keep Fusion happy and make it easier to access and update libraries in the cloud, remove all the local folders Fusion is configured to look in for libraries. For Design rules and CAM files, I suggest the following settings:

- Design Rules: `<path to>/QuadClass-Resources/Eagle/DRU`
- CAM Jobs: `<path to>/QuadClass-Resources/Eagle/CAM`

## Assembling the Schematic

You’ll build quadcopter in the cloud starting from a new Fusion360 electronics design called `quadcopter`. When creating this design, make sure to save it to the right team.

In this lab, you will create a schematic associated with this design, to be exported to the folder `hardware/quadcopter.sch`. Feel free to review [Lab 1](https://github.com/NVSL/QuadClass-Resources/tree/master/labs/Introduction-To-Eagle#exporting-files) for a refresher on exporting. You'll assemble the design by studying reference designs and the datasheets for the components you will use.

We will be sharing a library with you via the cloud called `quadparts_prebuilt_2022` located in `QuadClass-Resources\Eagle\lbr`. You will be reusing your `custom` library from last lab, and in this lab you will also create a new library called `LEDs`. These should be the only 3 libraries you use to assemble your schematic, Fusion360 comes with a bunch of built in libraries but they are off limits.

### General Schematic Style Guidelines

Here are the course style guidelines for schematics. Your schematics must adhere to these guidelines. If you don't, Eaglint will give warnings and we won’t accept the design.

1. All visible net and component names must not have “\$” in them. When Fusion360 automatically generates names for nets and components it includes “$”. This is fine if the name is not visible (e.g., on an anonymous wire between two components), but if you it shows up on your schematic, you should give it a nice name like `CTRL` or `SCL`.
2. By convention power supply symbols point up, and ground symbols point down. Neither should ever point to the side.
3. Nets should not cross each other unless they are electrically connected.
4. Nets should only be drawn at right angles.
5. Fusion360 embeds libraries in the `.sch` and `.brd` files. Make sure that you are keeping libraries up-to-date with `Library->Update...` or `Library->Update All`. We won’t accept designs with inconsistent libraries.
6. Include a frame around our schematic. Use device `FRAME_B_L`.
7. Use lines in `Info` layer to divide the frame into logically related regions (e.g., the IMU, the power supply, and the microcontroller). See the BBB schematic below for an example. Drawn nets shouldn’t cross these boundaries.
8. Use drawn nets connect components that are closely related (e.g., between the caps and the microcontroller in the BBB schematic)
9. Use named nets to connect separate “sub units” of your schematic. For instance, use drawn nets to connect all the capacitors to your IMU, but use named nets to connect your IMU to the microcontroller.
10. You should not use any libraries other than `quadparts_prebuilt_2022`, your `custom_*`, and your `LEDs` libraries.
11. Schematic symbols and wires should all be aligned to 0.05in grid (or, if you like, a 0.1in grid).
12. Labels for nets (created using the 'label' tool) should need to placed on the net they label. This means the label's location (which is marked with a gray '+') needs to be on top of a corner or end of the net. This guards against "drifting labels" that seem to be attached to another net.

### Selecting Parts

The `quadparts_prebuilt_2022` library has lots of parts in it, many of which you won't use. I've provided specific guidance about which options to select below. For resistors and capacitors, you need to use 0805 parts not the smaller and harder-to-place 0603 parts.  You should also avoid the resistor packs.  They are hard to place and solder.  If the resistor you need is not available in 0805, you'll need to create it.

### The Microcontroller

Here's the schematic for a board called the Basic Breakout Board (BBB). It uses the same microcontroller as your quadocpter, but it does not include the voltage regulator. It's the reference design for your microcontroller and the radio. The design also includes the 1x6-pin programming header you can see on the bottom of the FCB. YOu don't need to include that header in your design.

Why did I give a picture of what you need to build? Because reference designs are a very common practice in real PCB designs. The most reliable way to convey design requirements is to provide a working design. Why reinvent the wheel?

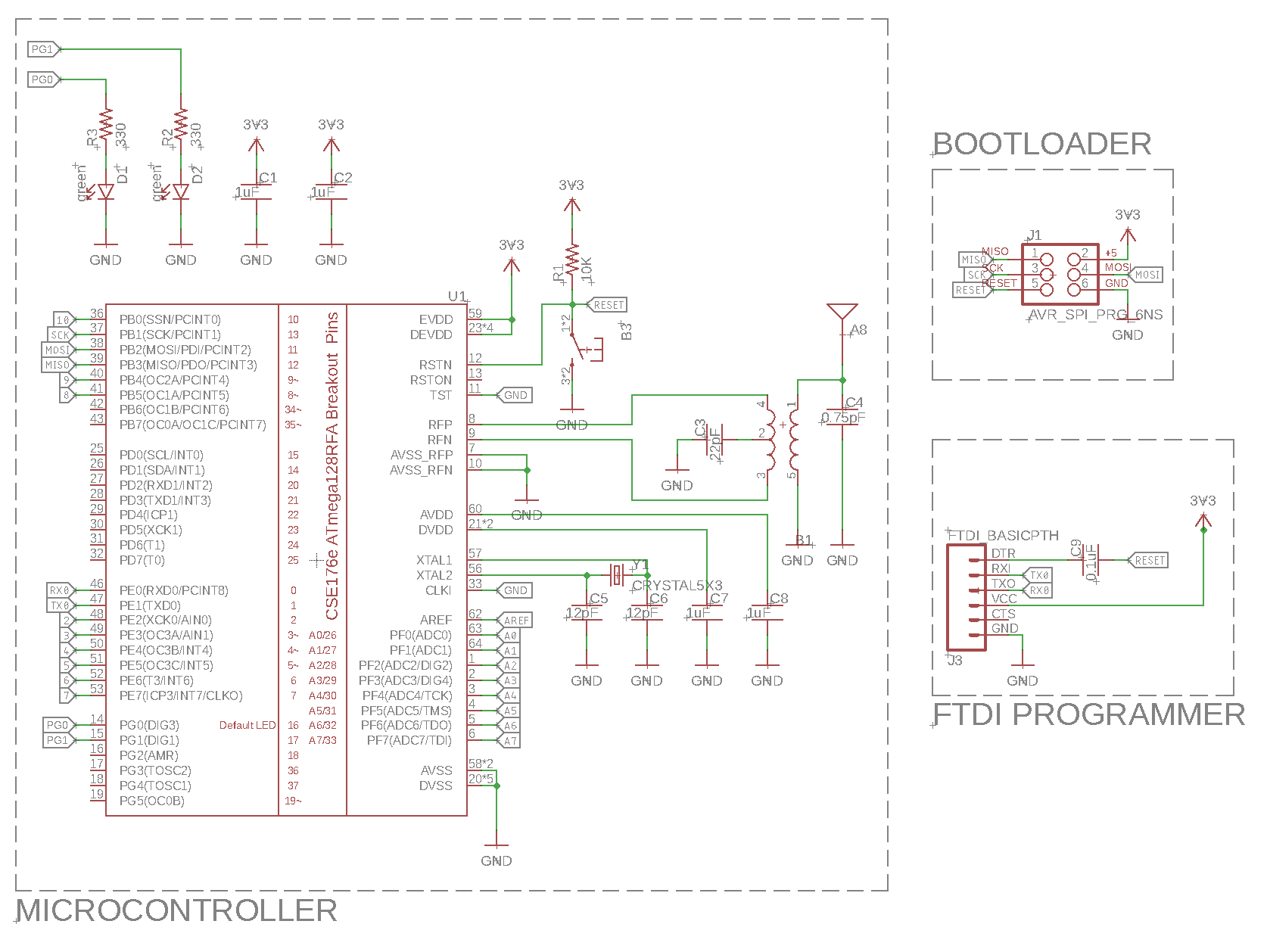
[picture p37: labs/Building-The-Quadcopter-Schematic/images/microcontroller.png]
Microcontroller schematic


You should use the schematic as a guide for constructing the microcontroller portion of your schematic. Build it from parts from `quadparts_prebuilt_2022` libbrary:

1.  Use one of the `-BOARD...` variants for the antenna. There's a left and right-handed version. Depending on your ultimate board design, you might want one or the other.
2.  `B1` is a 'balun'. Pay attention to the pin numbers.
3.  Use the `0.45x0.45` button.
4.  Replace one of the green LEDs with your red LED.
5.  You can use either variant for the `AVR_SPI...` header. The surfacemount one takes up more space (see it on your remote, under the LCD). The throughole one is more compact.
6.  You won't need the FTDI portion of the design.
7.  Do not connect the power pin on the ISP programmer/Bootloader header.
8.  Reference designs use different voltages from what you may want to use. Use 3V instead of 3V3.

You might notice that some of the symbols for the parts seem backwards. This is because they are 'mirrored'. There's a mirror tool or your can mirror parts by editing their properties with the `info` tool.

There are some changes you will need to make to this schematic based on what's required by the other components. This is just a starting point for your circuit.

If you have questions about the parts attached directly to the microcontroller (including the radio), the first place to turn is the microcontroller datasheet.

### Programming Header

Your quad will use a 4-pin programming header to load code into the MCU. You won't need the FTDI portion of the reference design. It's a little fancy since it allows you to insert the cable from either top of the board _or_ the bottom. To this end, use the `-FEMALE-SMD-BOTTOM-ENTRY` part from `quadparts_prebuilt_2022`. The four signals must appear in this order:

1.  Serial TX
2.  Serial RX
3.  GND
4.  Reset

These are a subset of the signals that connect to the FTDI header in the microcontroller reference design. You don't need the FTDI header. Note that you do need the 0.1uF capacitor between the reset line and the reset pin on the programming header.

### The IMU

The IMU datasheet contains all the information you will need to use connect the IMU to the microcontroller. A few things to keep in mind:

1. The IMU datasheet is not the best. If something doesn't make sense search the pdf.
2. There are actually two logical devices in this package: the accelerometer/gyroscope (referred to as 'A/G' in the datasheet ).
3. Both devices will operate in I2C mode only and connect to microcontroller via I2C, so you can ignore the stuff in the data sheet that refers to SPI.
4. The IMU has different connection modes. Follow connection mode 1 for your design, which is referred in `7.1 LSM6DSO electrical connections in Mode 1`, page 35.
5. You must follow all the recommendations regarding external capacitors attached the IMU, also known as decoupling capacitors.
6. You will need to take care of configuring the IMU's I2C addresses. Read section `5.1.1 I2C Serial interface`, pages 17 and 18, to determine which I2C address you can use. Use `Table 19. Internal pin status`, page 38 column Mode 1, to figure out which pin is dedicated for selecting the I2C address. You choose which address you want to use, but the address you choose needs to be reflected in your, otherwise your software won't be able to communicate with the IMU.
7. We aren't using the interrupt features, so you can leave `INT1` and `INT2` disconnected.
8. Power supply voltage (`Vdd`) and IO voltage (`Vdd_IO`) will be 3.0V in our design, so connect both to `3V`.
9. Connect `SDX` and `SCX` to GND.
10. We want the I2C to be always enabled. Determine if `CS` (Chip Select) should be connected to 3V (1) or GND (0) by reading "Table 1. Pin Description" in the IMU datasheet. Keep in mind that the IMU can work in diferent modes, we want mode 1. 

A thing to know about datasheets: They almost always (although, frustratingly, not always) tell you everything you need to know. They don't, however, make it easy. You need to read carefully and thoroughly. You can't skim the datasheet and expect to know the details of how to connect each of the pins to configure the IMU properly. You actually need to read through the tables and the text, there are specific answers to most questions you might have in there. Most facts appear exactly once in the datasheet -- it will be written in text or a table, but not both.

### The I2C Bus

Your MCU will communicate with the IMU via I2C. This means you must connect the IMU to the MCU via the `SDA` and `SCL` lines. You should "pull up" these lines to `3V` by connecting them to `3V` using 10kOhm resistors. Read section `7.1 LSM6DSO electrical connections in Mode 1`, page 35, to know how the pull-up resistos must be connected.

### The Motor Driver

Here's a picture of the motor driver circuit:

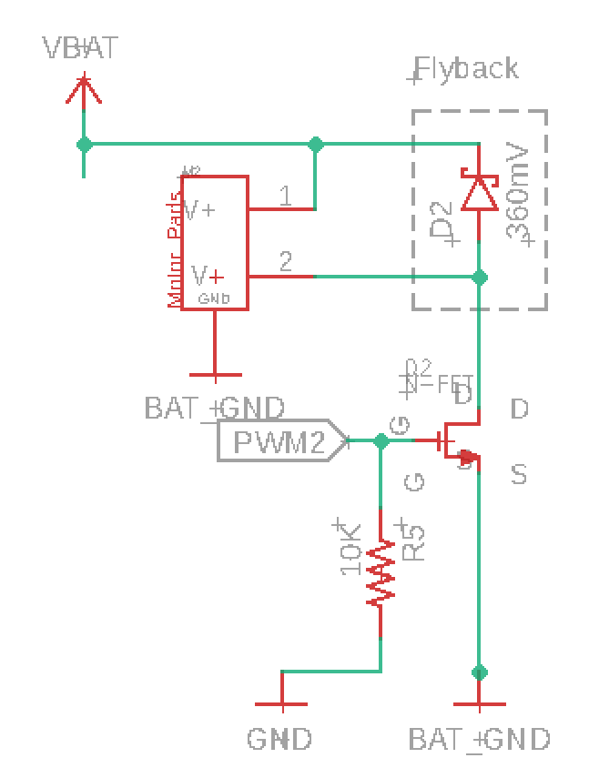
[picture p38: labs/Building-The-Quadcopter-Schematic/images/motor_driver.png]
Motor Driver


Build four copies to drive the four motors you'll need. All the parts you need are in `quadparts_prebuilt_2022` or your `custom` libraries.

1. Use the `-SMD-SOD123` diode in the library.
2. Use the `-MOLEX-SMD` variant of the `MOTOR_PADS_GND` device of the motor connector.
3. Use your MOSFET, of course.

The ground pin on the motor pads is not actually connected to the motor. It just goes to the metal "feet" that hold the connector down. You can see them on your FCB.

You'll need to connect the PWM control lines to suitable pins on the microcontroller. The suitable pins are marked with "~" on microcontroller's schematic symbol.

You need to include one 47uF decoupling capacitor between `VBAT` and `BAT_GND` (just one; not one per motor). It's to help absorb switching noise from the motors. Note that 47uF capacitor in the library is polarized. In the schematic the curved "plate" on the symbol should be connected to ground.

### The Power Supply

The quadcopter draws power from from a LiPo battery that nominally provides between 3.7 and 4.2V. This voltage is too high for the IMU and the microcontroller. Also, the motors (which we will power directly from the battery) will create all kinds of noise on both the battery supply and ground rails. To solve both of these problems, we will use a low-dropout (LDO) voltage regulator to provide a stable 3.0V power supply to the IMU and the microcontroller.

As a result, your quadcopter will have two power rails: An unregulated power rail (called `VBAT`) that provides power to the motors and input of the voltage regulator and is driven directly by the battery, and a regulated supply driven by the voltage regulator (called `3V`).

The power supply for quadcopter needs to contain the following parts:

1. The battery. This is the `BATTERY` device in `quadparts_prebuilt_2022`. You need to use the `-SCREW-TERMINAL` variant.
2. A LP3985-series 3.0V regulator (see device `TPS73633-DBVT`. Don't use the 3.3V or 2.5V variants, use the 3.0V variant).

Check the votage regulator datasheet (in `Datasheets`) for guidance about what kind of capacitors to connect to the regulator and how. Wire the enable line to `VBAT` and don't connect anything to `NC/FB`.

You will also incorporate a power switch for the quadcopter. The switch will connect the `EN` pin of the voltage regulator to `VBAT` when it's turned 'on' and connect `EN` to `BAT_GND` when its turned 'off''. Use the `-SMD-EDGE` variant of `POWER-SWITCH-MFS201N-9-Z` for the switch.

You'll note that the output of the voltage regulator has decoupling capacitors on. This keeps the voltage regulator stable and filters out noise on the output. Experience shows that quickly turning on the motors can causes the output of voltage regulator to drop enough to reboot the MCU. Add an additional 47uF decoupling cap (the same one we use for motors) to the output of the voltage regulator between `3V` and `GND` to prevent this. Note that the 47uF capacitor is polarized. The flat plate should connect to the positive voltage, and the curved plate to ground.

To the extent possible, we need to isolate the the IMU and the microcontroller from the noise that the motors will create on the power supply lines. The motors will cause noise on both their power supply ( `VBAT` ) and ground return lines, so we will provide them with separate power and ground lines. For the power line, this is easy: Just connect the power supply for the motor drivers directly to the battery's positive terminal.

For the ground line, it is more challenging, since all the devices on the quadcopter must share a common ground reference. The best we can do is to structure our schematic so that we can exercise tight control over how the ground line is laid out on our PCB. To do this, create a separate ground net that connects the ground terminals of motor controllers to each other and the negative terminal of the battery (call it `BAT_GND` and use the `BAT_GND` device in the `quadparts_prebuilt_2022` ). Then connect the digital ground (i.e., the ground that connects to other components, aka `GND` ) to the battery ground using a schematic component called a "net bridge" (see below). We will see in the next lab how we can use this structure to isolate the digital components. (This is a very important step, and we added it to fix problems that occurred in all but one of the quadcopters we built in this class the first year it was offered).

A "net bridge" is a PCB part whose only purpose is to electrically connect two nets in a schematic while keeping the nets separate in schematic (i.e., the two nets keep their own names). To create a net bridge, create a device with a footprint that consists of two SMDs that touch one another and a sensible schematic symbol for what is, in essence, a wire. Put it in your `custom` library. The SMDs can be very small (e.g. 0.5mmx0.5mm). Remove the `tStop/SolderMaskTop` and `tCream/StencilTop` on the pads, since we won't be soldering anything to them. You don't need `tKeepout/ComponentExcludeTop` anything in `tPlace/SilkscreenTop` for the net bridge. If eaglint complains, just explain that it's not necessary since it's the net bridge.

Use bridge to connect `BAT_GND` and `GND`.

#### Basic Principle: Decoupling

Your quadcopter is full of transistors (small ones in your microcontroller and big ones in your motor drivers), and as they switch they cause noise on the power and ground planes. Noise on the power line can cause digital circuits to stop working (because 1’s start looking like 0’s) and noise on GND can cause all kinds problems because all voltages are measured relative to GND.

The minimize this noise, we want to increase the capacitance of the power and ground planes. One way to think of capacitance is as a resistance to changes in voltage, so adding more will reduce noise (which is an unwanted change in voltage). Small capacitors can filter out high-frequency noise, while larger capacitors filter out lower-frequency noise.

There are two ways to add capacitance. The first is to add capacitors. The IMU and the microcontroller both describe the number and kind of decoupling capacitors you should incorporate and they tell you to place them as close as possible to the power and ground pins on the device. This is because, to be most effective, the extra capacitance we add needs to be as close to the source of the noise as possible (to minimize resistance and inductance between the cap and the device).

The second way to add capacitance is to build a capacitor into the board. A capacitor is just two layers of metal separated by an insulator. We can easily construct this in a PCB by laying down metal in two layers on top of eachother, and connecting one to power and one to ground. The result is a very small capacitor but one that we can put nearly everywhere on the PCB (so it will be a close as physically possible to the devices). In our design this capacitance is not critical, but in higher-speed design, it is critical to filtering out the higher-frequency switching noise.

### Breakout Headers

You will face a couple challenges in bringing up your board and it's good to plan for them now. Do this by adding a debugging header to your design. "Headers" are exposed connections to signals on your board. You can attach pins or sockets to them as needed to help in debugging.

#### Signal Breakouts

When your quadcopter comes back from manufacturing and you assemble it, some debugging may be necessary and that may include the need to measure what's going on in different parts of the circuit. To make this easier, I suggest including a debugging header in your design.

A debugging header is a set of pins that connects key signals to pins that you can easily probe during debugging. I suggest including the following signals:

- `GND`
- `BAT_GND`
- `VBAT`
- `3V`
- The control lines to the four motors
- `SDA`
- `SCL`

There's a 10-pin header in the library you can use for this. You can also break up the debug header into smaller headers. For instance, you could put a 3 pin header next to each motor with `VBAT`, `BAT_GND`, and the control line. It's always a good idea to include a ground on each debug header.

Debugging headers can be a little dangerous to use, because it can be easy to accidentally create a short circuit between two of the pins when you are debugging (e.g., by touch both pins with a probe). This is especially dangerous if you connect a power net and a ground net. To avoid this, intermingle the PWM, SDA, and SCL lines with the power and ground lines, so that no power pin is next to ground pin.

#### IMU Rescue Header

Soldering the IMU is hard enough that it causes a fair number of
quadcopters to fail. To guard against this, add a header that will
allow you to connect this breakout board
(https://www.adafruit.com/product/4438) to your quadcopter. You are only required to
four pins: `3V`, `SCL`, `GND`, and `SDA` (not necessarily in that order. Look at the breakout board it must connect to to figure out the order.). These pins are conveniently
located next to each other on the breakout board. Use the 1x4 4-pin female header in `quadparts_prebuilt_2022` (not the `2x2`).

If you feel like being efficient, you can leave `SDA` and `SCL` off the signal breakout header, since they are on the rescue header.

### Battery Voltage Meter

You can monitor the batteries voltage using a voltage divider and one of the MCU's analog pins (https://learn.sparkfun.com/tutorials/voltage-dividers/all). The basic idea is to divide the battery voltage (4.2V max) so that the maximum output of the divider is less than 1.8V. Then you can measure the that voltage with one of the MCU's analog inputs.  Your divider should be between `VBAT` and `BAT_GND` (You can connect it to `GND` instead, if you like, but Eaglint will complain.).

You should use large resistances in your divider (e.g., in the kOhms range) so that not much current flows through it.

### Some LEDs

You should also add some LEDs to your design. There are several reasons to add LEDs to your design:

1. It'll make it easy to tell which end of your quadcopter is the front.
2. They look cool.
3. They can provide information about what's going on in your flight control software.

There are several options for powering and/or controlling LEDs:

1. You can connect them to the output of the power switch. In this case, you can't control them and they can be very bright. You need limit the current for the LEDs to 300mA (the capacity of the switch).
2. You can connect them to pins on the micro controller. If you use a digital pin, you can turn them on and off. If you use a PWM pin, you can control their brightness. In either case, you must size the resistor properly to limit the current through the LED to 8mA (the limit on the per-pin current on your microcontroller).
3. You connect them to battery power and turn them on and off using a transistor connected to a microcontroller pin. Depending on the pin you use, you can turn them on and off or vary their brightness. The transistor we use in the motor controller should work fine. If you do this, you can drive multiple LEDs with the same transistor and pin.

If you drive LEDs with a MOSFET, you should include a 10kOhm pull-down resistor to `GND` on the gate of the MOSFET.

Regardless of which approach you take, you will need to pick out your LED. To do this, go to http://digikey.com. And enter LED into the search field. You'll see a bunch of results. Likely candidates for smaller LEDs are to be found under "LED Indication - Discrete," while brighter LEDs can be found under "LED Lighting - White", "LED Lighting - Color".

You'll note there are a dizzying array of options (at this moment there are over 20,000 different indicator LEDs available). Digikey presents you with a decent searching interface. Go exploring! Things to keep in mind:

1. Any LED you choose needs to be available in small quantities (the "minimum quantity" column should say "1").
2. The need to be at least 0805 (1.25mm x 2mm).
3. They need to be reasonably cheap: no more than $1 per LED.
4. The LED needs to be available in quantities of 1 and it needs to be in stock.
4. If you are going to drive the LEDs directly with a microcontroller pin, you must limit current to 8mA and you should make sure that the LED will actually light up with 8mA (many bright LEDs will not).
5. They need to be compatible with the power supply you are going to use: 3.7-4.2V if you use the battery. 3.0V if you are going to drive them from the microcontroller.
6. Their current draw needs to be within the limits of how you are powering them.
   1. The microcontroller limits how much current each pin will supply.
   2. The microcontroller consumes some current, as does the IMU (check the datasheets).
   3. The voltage regulator has limits on how much current it can provide.
   4. Make sure that voltage regulator can handle all your LEDs in addition to the microcontroller and the IMU.
   5. If you are powering them with VBAT, limit total current draw for all your LEDs to 500mA.
7. The current draw depends on forward voltage. The LED datasheets will contain some graphs that relate voltage to current and current to brightness. Pay attention to them to make sure that a) you aren't drawing too much current and b) your LEDs will light up.
8. There are many different parameters to consider: Color, brightness, viewing angle, etc. You'll need to go learn about these by reading the datasheets, etc.
9. You will probably want surface mount parts, but you can also use through-hole if you want.
10. Digikey lists the typical forward voltage on the web page. The LED will work with larger or smaller voltages (up to a point. See the "absolute maximums" section of the datasheet for limits).
11. If the forward voltage of the LED is much lower than the supply voltage, you'll need a large resistor to limit the current. Alternately, you could put two (or more) LEDs in series. The total voltage drop across the LED(s) and resistor needs to be greater than or equal to the supply voltage.
12. You can use RGB LEDs, too. Checkout the datasheets for details.

You'll need to build the library entries for the LED you want to use and then integrate them into your schematic. You'll also need to include a current-limiting resistor. You'll need to use Ohm's law to calculate the correct resistor value (here's a tutorial: http://www.ohmslawcalculator.com/led-resistor-calculator). You will also need to be sure that resistor can handle the amount of power it will need to dissipate (see the datasheet). If our libraries doesn't include an appropriate resistor, you'll need to add one from the same family of resistors we are already using (check the datasheet for the resistors in `quadparts_prebuilt_2022`). Make sure it's available in small quantities on Digikey. Put the new resistors in `custom`.

One thing to keep in mind is that most LEDs are extremely bright when driven at full current. Indicator LEDs can be driven very gently and still be visible. LEDs added for visual effect can be driven harder, but they can easily become so bright that you can't even look at your quadcopter without being blinded. For this reason, any LEDs that you want to be bright need to be attached to PWM pins, so you can moderate their brightness.

It can be a little hard to tell from the datasheets how bright LEDs will be actually be.  There's often a "luminous intensity" entry in a table that measured in [millicandelas](https://en.wikipedia.org/wiki/Candela) (`mcd`).  The definiton of a candela is a little complicated.  There is usually a graph that related luminous intensity to current, but it's "relative" luminous intensity, so it just tells you how the brightness will vary with current.  It doesn't say how bright it will be.

Once you have picked your LEDs, document your LED design using text in the `Info` layer in your schematic. For each type of LED, you should note its forward voltage, the resistance of the current limiting resistor, the current you expect to flow through the LED, and the power you expect it to disipate (power = current * voltage).

Feel free to get creative with the LEDs! Smilely faces. Simulated space ship engines. Aircaft "running lights". Dance party. Ground effects.

Put the LEDs devices/footprints you create in a new cloud library called `LEDs`. Reuse the LED symbol from `quadparts_prebulit` or your `custom` libraries.

The footprints/devices you build need to meet all the standards described in `Building Parts in Fusion360 Lab`.

Add an attribute called `CUSTOM` to the variants you create. It should be constant but without a value. This will ensure they get ordered.

#### Reference design LEDs pin numbers

When you add your LEDs, you may want them to follow the same pinout as the FCB. From the "Programming the Hardware" "Blinking the LEDs" lab section, you know the soft pin numbers for addressing the LEDs in software, but you may not know the pin and pad numbers these pins are connected to in the schematic and board. Below is a reference table for LEDs, we also added free PWM pins you can use:

| Ref NAME | Type | In FCB | Soft Pin (Arduino) | Pin (Sch) | Pad (Brd) |
| --- | --- | --- | --- | --- | --- |
| LED 1 (RED) | Digital | Yes | 16 | PG0(DIG3) | 14 |
| LED 2 (GREEN) | Digital | Yes | 17 | PG1(DIG1) | 15 |
| LED 3 (ORANGE) | Digital | Yes | 18 | PG2(ARM) | 16 |
| LED 4 (BLUE) | Digital | Yes | 36 | PG3(TOSC2) | 17 |
| PWM 1 (PRETTY_LEDS) | Analog  | Yes | 34 | PB6(OC1B/PCINT6) | 42 |
| PWM 2 (FREE) | Analog  | No | 9 | PB4(OC2A/PCINT4) | 40 |
| PWM 3 (FREE) | Analog  | No | 19 | PG5(OC0B) | 19 |
| PWM 4 (FREE) | Analog  | No | 35 | PB7(OC0A/OC1C/PCINT7) | 43 |

### Eaglint

Your design needs to pass http://eaglint.nvsl.io, so commit your design, submit it, and fix the problems it finds. Remember, each time you run a full check with the tool it lowers your grade on the lab, so you need to check your design carefully before submitting.

### Things to remember

1. Remember to sync your libraries with your schematic: `Library->Update All`.

### Things to Submit

Include these in your github repo:

1. Your `hardware/quadcopter.sch`.
2. Your `hardware/lbr/LED.lbr`.
3. Your `hardware/lbr/custom.lbr` (maybe renamed to `custom_<name>.lbr` and maybe two of them)
4. Datasheets for your LEDs in `hardware/datasheets/`.

Feel free to consult [Lab 1](https://github.com/NVSL/QuadClass-Resources/tree/master/labs/Introduction-To-Eagle#exporting-files) for export guidelines.

Submit it to Eaglint: http://eaglint.nvsl.io.

For this part of the lab, human review will succeed instantly, if you have no errors or warnings.

## Turn in Your Work

"Perfect" score: 10

Initial points: 12

Quick checks are free. Full checks cost 0.5 points. Submitting for human review costs 0.5 points. Each day late costs 1 point.

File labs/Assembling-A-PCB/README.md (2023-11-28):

# Assembling Your Quadcopter

Assembling your quadcopter is similar to assembling the charger board, but more involved because there are more components.

## Preparation

Assembling a board (especially your first one) can take a couple hours.  Also, the working time for the solder paste is limited, so you need to work reasonably quickly once you start.

Begin by making sure you have everything you need.  For the quadcopter assemmblies we will, have everything you need set up ahead of time.

## Safety

The solder paste we use (like all solder paste) is potentially toxic (although it's lead-free).  The material safety datasheet is here: [MSDS](../../Datasheets/NP560_SDS_EN_(V3)US.pdf).

You must take the following precautions:

1.  You must wear eye protection while applying the paste or using a soldering iron.  The makerspace has glasses across the hall from our classroom.  Your own glasses are fine.
2.  You must wear gloves while applying paste and placing parts.
3.  You must not eat or drink while working with solder paste.  During assembly labs, no food or drink is allowed in the classroom.
4.  You must wash your hands before eating or drinking after the lab.

## Preparing Your Part Kit

You can think of the part kit for your quadcopter as breaking into three parts:

1.  The parts that are common to all the quadcopter designs.
2.  Additional instances of the parts common parts.
3.  Parts specific to your design.

For the first group, we have part packets prepared for you just as we did with the BBB board.  Grab *one* of each packet.

The second group is usually resistors and mosfets (e.g., to control LEDs).  Take additional packets of these parts to get what you need.

For the third group, we have ordered parts from Digikey for you.  Each part will come in it's own bag with the "customer reference" field containing the list of reference designators that the parts correspond to.

## Assembly Drawings

Eagle provides a simple mechanisms to help you place parts.  Open your `.brd` file.  You need to enable  the "Design Manager" (`View->Design Manager`).

The "Devices" pane shows a list of all the parts in your design.  Sort the list by "value" and hide the other columns (wrench icon).

You can now select all the parts of a given type and Eagle will highlight their location on the board.

## Applying Solder Paste

### What You Need

1. Blue tape
2. Solder stencil
3. 4 scrap PCBs the same thickness as your board. 
4. 1 large putty knife
5. 1 small putty knife
6. Butcher or craft paper
7. Gloves
8. A magnifier
9. Alcohol in a pump dispenser
10. Kimwipes
11. Compressed air
12. Solder paste
13. Gloves

### Preparing Your Space and Aligning Your Stencil

You need a large, clear space to apply solder paste.

1. It can be messy, so cover everything with a big sheet of butcher or craft paper.  Tape down the paper, so it's not sliding around.
2. Tape down some scrap PCBs so they will hold your board still.  The PCB should be oriented so the stencil aligns with it in "portrait" orienation (tall rather than wide).
3. Align your stencil with your board so the wholes line up perfectly with the pads. This must be very precise.
4. Tape down the right edge of your stencil so you can easily lift it on and off your board like a page of a book.  The tape should be on the right, and there should be clear space for the stencil to lay flat.  
5. Check the alignment again
6. Verify your alignment with course staff.

### Apply Paste

1. Use the narrow putty knife to apply a thin (1cm) bead of paste to the edge of the wide putty knife.
2. Hold the wide putty knife at a 45-degree angle and drag it across the stencil, using firm (but not too hard), constant pressure to apply a thin layer of paste across across the stencil.  Press just firmly enough that there is a thin layer of paste left on the stencil (see photo).  If you push too hard, it will force paste through and slightly under the stencil, which is not what you want.  Move smoothly.  Do not stop.  Make sure you align the knife so it will pass over all the pads on the board.  You can only make one pass.
3. Turn the squeegee over and scrape the extra paste off the stencil with the squeegee almost vertical and held gently against the stencil.  There should be very little paste left.  Again, you can only make one pass.
4. Smoothly and in one motion lift up the stencil and fold it back.  Lifting it up and accidentally dropping it back onto the board is means redoing it.
5. Examine the paste pattern with your magnifier.  Look out for
   * Pads with missing paste
   * Indistict or touching -- even slightly -- paste blobs (esp. on the IMU, microcontroller, and balun).
6. Check it with course staff and point out any problems you spotted.
7. If it looks good, carefully remove your board.
8. If something is wrong, you'll need to remove all the paste using Kimwipes and alcohol and start again.  You can do this many times.
9. You need to be very exacting about paste application.  The solder needs to be very crisply defined.  If it doesn't look good, you'll have to redo it.  Redoing it is not hard, and it's good practice, so there's no point in settling for sub-standard paste application.

**A Stencil**

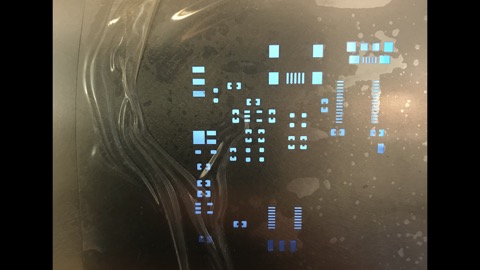
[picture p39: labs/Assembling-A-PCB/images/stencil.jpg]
Stencil


**Poor Stencil Alignment (some holes are dark)**

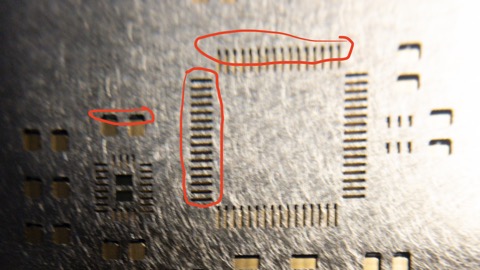
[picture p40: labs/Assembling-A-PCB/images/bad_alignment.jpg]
Poor stencil alignment


**Good Stencil Alignment (all holes are gold)**

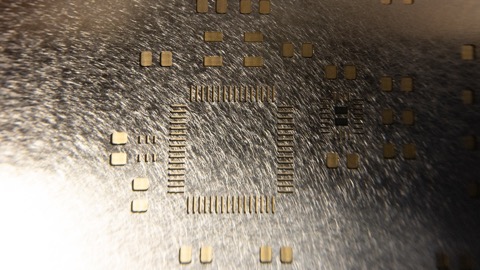
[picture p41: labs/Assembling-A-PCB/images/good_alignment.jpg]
Poor stencil alignment


**Poor Paste Application**

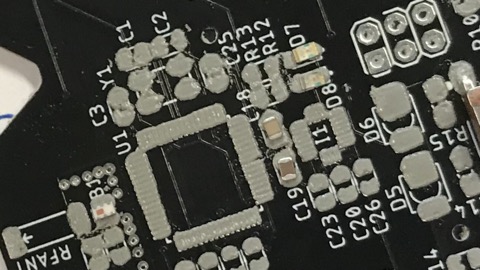
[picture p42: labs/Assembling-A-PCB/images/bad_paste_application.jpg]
Poor solder paste


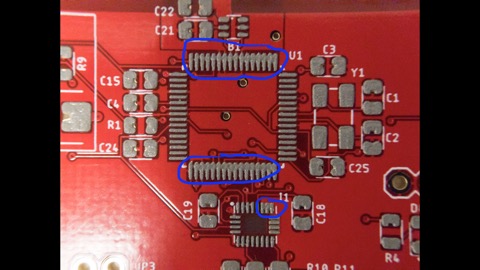
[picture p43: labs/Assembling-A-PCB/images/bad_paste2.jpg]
Poor solder paste


**Good Paste Application**

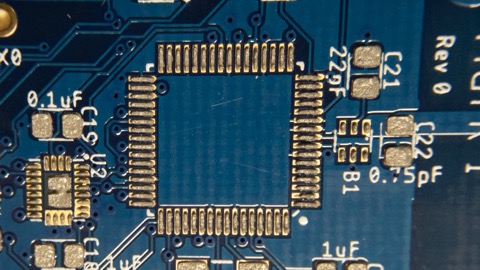
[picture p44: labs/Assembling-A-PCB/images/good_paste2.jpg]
Good solder paste


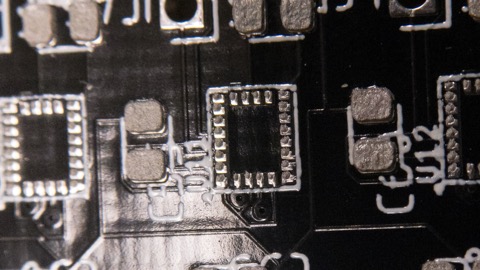
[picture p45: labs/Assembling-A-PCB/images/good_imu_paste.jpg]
Good solder paste


### Cleanup

1. If someone else is going to use putty knifes immediately, you can leave them.
2. If not (or in doubt), clean them by scraping large blobs of paste back into its container and wiping them with alcohol and kimwipes.
3. Wipe up any stray solder paste on the table, *both* sides of the stencil.
4. Blow any remaining solder paste out of the stencil holes with compressed air.

## Placing Components

### What You'll Need

1. A complete part kit for your board.
2. A pair of tweezers
3. A magnifier.
4. Steady hands.

### Get Organized

You need to place parts carefully and precisely.  You also need to work somewhat quickly.  With practice, you can place a board like the charger in 10 minutes.  You should not take more than an an hour to do your quadcopter.  Getting organized will help you meet this goal.

1. Get _everything_ you need together at once.
2. Collect all the parts you will need (see below). 
3. Have a clean work area (preferably with a white surface).  The parts are _tiny_.  The less stuff there is around, the less likely you are to lose anything.
3. Allow adequate time.  
    * Paste has a limited working time, and the course staff are not around forever.    
    * For the quadcopter, assembly will probably take ~1.5 hour.  Reflowing takes ~12 minutes.  Something will go wrong, budget an extra ~15min.  
    * So, you need to start assembly at the beginning of class.
5. Eat something before hand.  You need to patient and steady.

### Placing Parts

1.  Dump the parts from one a packet out on your work surface.
2.  If a part is upside-down, picking it up and dropping it is a good (if probablistc) way to turn it over.
3.  Place the part gently and as precisely as you can.
4.  Once the part is on the board, move it as little as possible.  Moving the parts smears the paste.  The parts will self-align a bit during reflow, so it doesn't have to be perfect.
5.  Don't pick up the board.  You more likely to bump a part if you pick up the board.
6.  Arrange your pile of parts at your board so you don't have to reach over the board, otherwise, you're more likely to bump parts.
7.  Don't mess up.  If something goes significantly wrong, you have to start again.
8.  Do one type of part at a time (e.g., 1uF caps).  You should have exactly the right number of them, so when they are gone, you're done.
9.  Typing `show C1 C2 C3` in Eagle will highlight where `C1`, `C2`, and `C3` are on the board.   You can also say `show C*` to see where all the caps are.  
10.  Place the parts very gently onto the board.  It should almost be like you are dropping them.  Do not press them down.  It'll displace the solder paste.
11.  If you think you've messed things up, get the TA or prof.  They may be able to save you...or not.

### Notes on Particular Parts

I suggest you proceed in this order.  This is roughly from easiest to hardest.

Note that on the remote, there are many parts you will leave unpopulated. Only put parts where there is solder paste.   

In the photos, I've highlighted the polarity markings on the board and the part.

#### Resistors

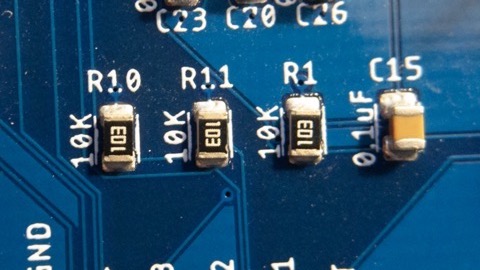
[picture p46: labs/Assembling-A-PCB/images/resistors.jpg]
Resistors


1. These are pretty easy -- a good warm-up.
2. Make sure they are marking-side-up.

#### Capacitors

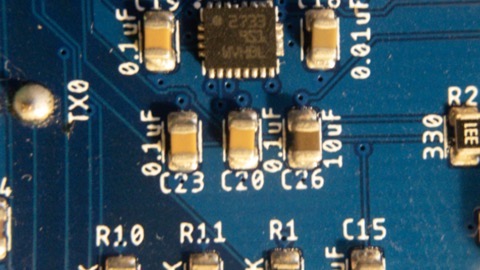
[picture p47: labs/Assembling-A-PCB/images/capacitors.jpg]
Capacitors
1.  The small caps are non-polarized, so direction doesn't matter. 
2.  Align the big caps carefully.  If you get it wrong your board will look ugly.
3.  Far the 47uf caps, orientation is important.  The end with the stripe of color goes in the "cup" on the footprint.

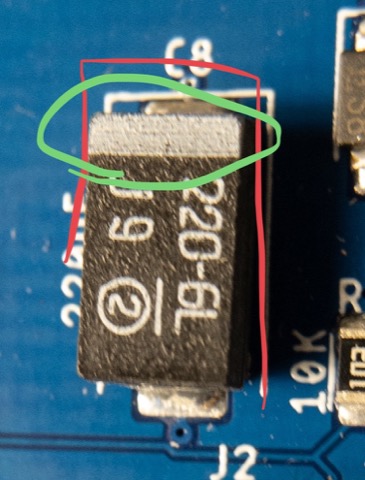
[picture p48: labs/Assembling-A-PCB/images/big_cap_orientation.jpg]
Caps
  

**Good Cap Placement**

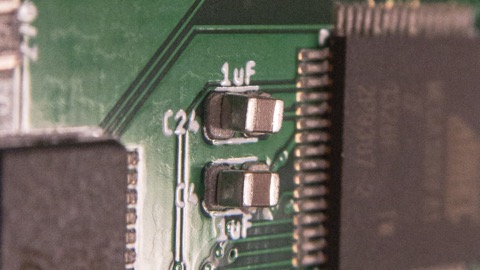
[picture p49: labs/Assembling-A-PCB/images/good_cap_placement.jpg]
Good cap placement


#### Voltage Regulator
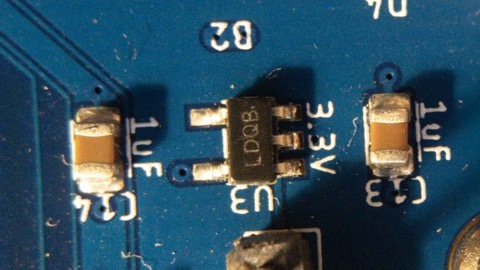
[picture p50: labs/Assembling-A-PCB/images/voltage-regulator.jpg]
Voltage Regulator


1. Orientation is obvious (there's three pins on one side and 2 on the other)

#### Button 

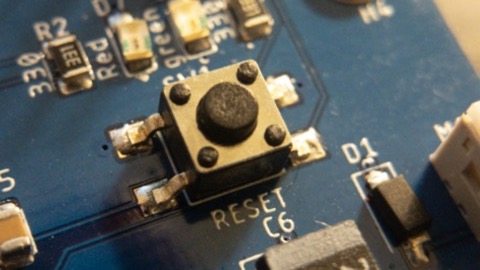
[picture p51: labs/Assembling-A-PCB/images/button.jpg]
Button


1. Either orientation is ok.

#### Crystal

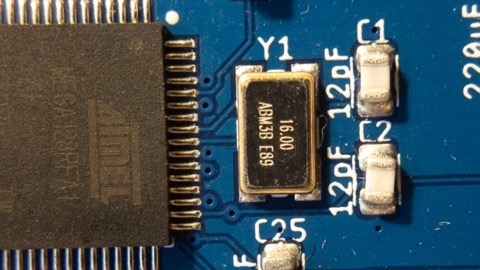
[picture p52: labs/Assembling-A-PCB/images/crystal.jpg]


1.  It seems like orientation should be important, but it's not.  The part is diagonally symetric. 

#### LEDs

1. This is your first polarized component, pay close attention or your board will be doomed to darkness.
2. The green line (yes, there really is one) goes near the dot. 

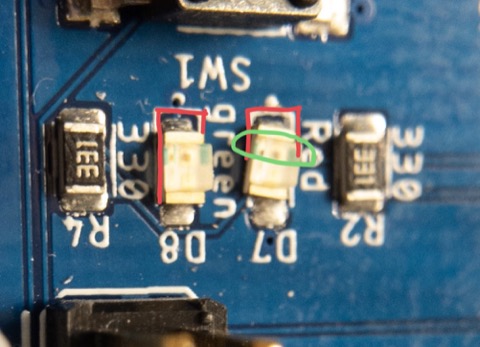
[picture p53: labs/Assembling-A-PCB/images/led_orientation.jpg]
LED orientation


#### Diodes

1. These are  polarized, but the markings are extremely hard to see.  They are printed black on black.
2. If you hold the diode and look at in the light, one end has a faint rectangular bar code on it.  The other has an "8"
3. The barcode goes near the dot.

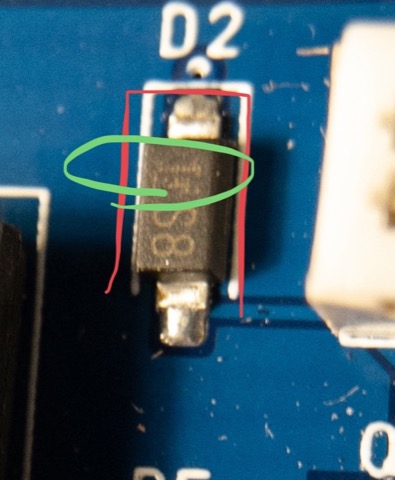
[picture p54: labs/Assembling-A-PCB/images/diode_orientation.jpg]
Diode orientation


#### Balun

1.  The red dot faces up and goes next to the dot.  This means the red dot will be farther from the microcontroller and nearer the antenna.
2.  Pay close attention to the aligment.
3.  Check it with your magnifier.

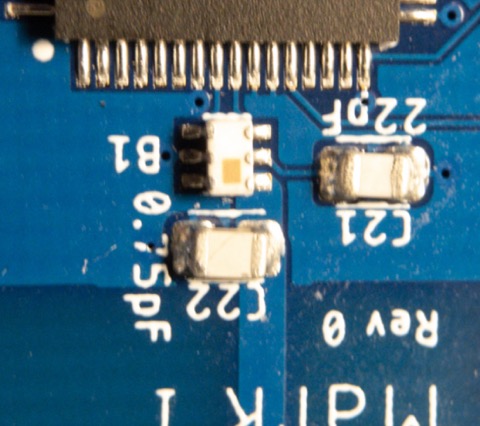
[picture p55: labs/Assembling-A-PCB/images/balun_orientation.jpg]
Balun orientation


#### Microcontroller

1.  Make sure you orient it correctly.  The dot goes next to the dot.
2.  The silkscreen markings fit tightly to the corners of the package, so use them as a guide. 
3.  Once it's down, check the alignment.  If it's not perfect, do not pick it up.  Instead, nudge it every so gently to align it.
4.  The magnifier will help you check alignment.  You can see the pads on the side of the package.  The pins on the package need to be aligned with the patches of solder paste on the board.

**MCU Alignment**

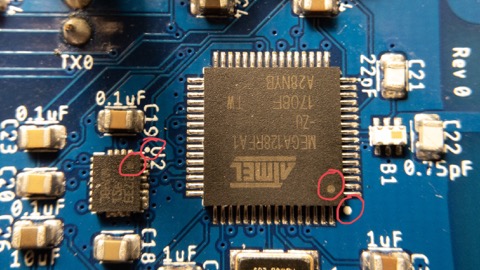
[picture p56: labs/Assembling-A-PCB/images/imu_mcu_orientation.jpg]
MCU orientation


**Good MCU Placement**

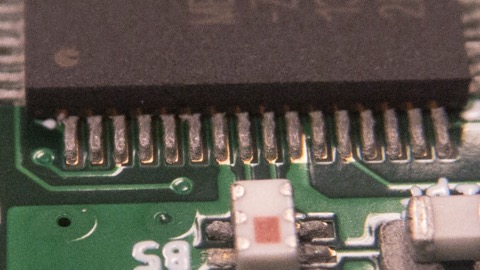
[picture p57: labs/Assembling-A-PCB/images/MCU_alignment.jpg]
Good MCU Placement


#### Battery Terminals

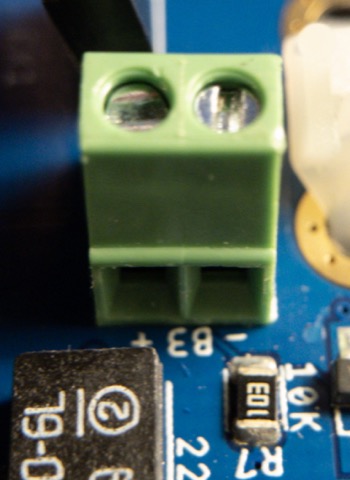
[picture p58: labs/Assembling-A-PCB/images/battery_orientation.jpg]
battery orientation


#### MOSFETs

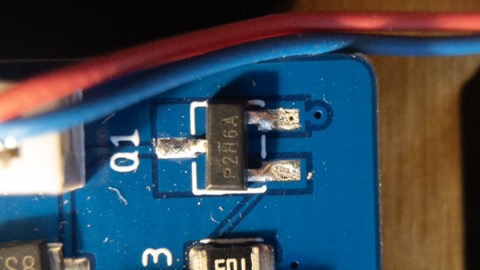
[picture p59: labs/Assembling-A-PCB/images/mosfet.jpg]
MOSFET


1. The correct orientation is obvious, since the package asymmetrical.
2. You need to align the pins carefully.

#### IMU 

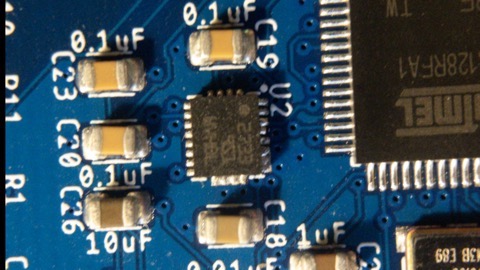
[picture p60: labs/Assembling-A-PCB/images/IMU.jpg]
IMU


1.  Similar to the microcontroller.
2.  The dot goes near the dot. (see image above for MCU)
3.  Use the silkscreen markers to align it and the "drop" it on.
4.  The pads are smaller, so alignment is more important.
5.  Don't fiddle!

## Reflow

### What You Need

1. A TA or professor.
2. The reflow oven.

## Touch Up and Throughhole Components

### What You Need

1. Soldering station.
2. A syringe of flux.
3. Thin, lead-free solder.
4. Swaps and/or a horse-hair brush.
5. Alcohol in a squirt bottle.
6. kimwipes.
7. Blue tape.

### Checking Soldering

**Good MCU Soldering**

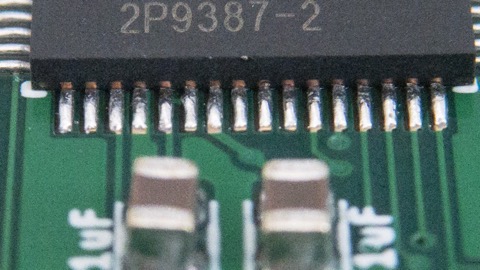
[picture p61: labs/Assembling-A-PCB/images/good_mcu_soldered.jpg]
Good MCU Soldering


**MCU Soldering Requiring Touch Up**

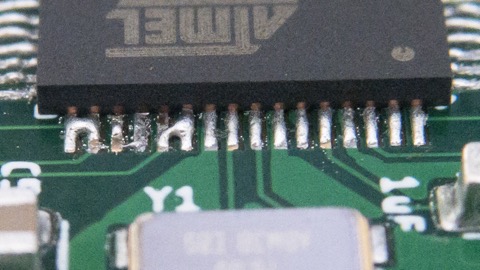
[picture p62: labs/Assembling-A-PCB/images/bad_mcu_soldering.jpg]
Bad MCU Soldering


1.  Similar to the headers, but orientation matters.  The holes on the side should point toward the '+' and '-' on the board.

### Cleaning up Flux Residue

Wire solder has flux in the middle to help the solder flow.  SMD rework requires adding flux manually.  In either case, the result is a yellow-brown, unattractive residue that starts out sticky and hardens over time.

To keep your board looking nice and clean, you should remove it ASAP.  If you have several things to fix, do not wait till the end.  Due it one part at a time.  To clean up the flux, place a kimwipe over the area and squirt rubbing alcohol onto it.  Then, take a hair brush of swap and rub the kimwipe around over the area.  It'll absorb the flux residue.  Repeat once or 
 twice.  Don't be shy with the alcohol, it won't hurt anything.

If you don't have alcohol in a squirt bottle, just get the kimwipe very moist with alcohol and put it on mannually.

### Mounting Throughhole Parts

You'll have to solder the through-hole parts by hand. The process is the same for all of them:

1.  The part goes on the side of the board with the reference designator.
2.  Tape down the part using blue tape. 
3.  The main challenge is getting them straight up and down and not crooked.  Do your best.

We aren't populating the big headers on the BBB to save time in class.

#### ISP Header

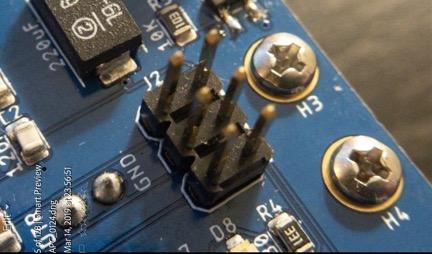
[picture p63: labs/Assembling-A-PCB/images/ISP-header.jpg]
ISP


## Time Management

Assembling your boards will take longer than the charger, because there are more parts, and class time is limited.  To ensure you have time to apply paste, place parts, and reflow the boards, you must start applying paste **at the beginning of class**.  

We will have stations set up for applying paste at 10am on days we are doing assembly for this purpose.

This means you need to have your part kit completely assembled **the class period before**.  If your part kit is not ready at the starte of class, we will not let you start assembly that day.

You also need to work quickly.  Your quadcopters have between 70 and 100 parts (vs 12 for the charger), and you need to complete assembly at least 1 hour before the end of class (2pm).  This means you need to be placing 1 part ever 30-45 seconds or so.  Keep an eye on the clock.

## Scheduling

On assembly days, the TA will set have parts out by 10am and paste assembly stations ready by 10:30.

On Tuesdays, you must have boards ready for reflow by 1pm. 

On Thursdays, we have to vacate the room by 1pm.  I would suggest starting (and finishing) assembly in the main maker space work area.  Again, you must be ready to reflow by 1pm.

The TA and I both have other obligations after class after on some days.  This means that if you aren't ready to reflow in time, we may not be able to stay after to reflow your board.

The soldering stations are available for hand-soldering the through-hole parts.  You can work on this whenever the maker studio is open.

## Tips, Tricks, Bells, and Whistles

### Attaching the Motors

The spec for the board, should provide a snug fit for your motors, but the board milling process is not perfectly precise.  Also, the motors are subject to significant stress during testing (as your board bangs around the test stand).  To hold the motors in place, hot glue works well.  Position the motors as you like and apply 1-2 _small_ amount of got glue to the corner formed between your PCB and the motor.   You don't need very much and applying alot will make a mess and make it difficult to remove the motors later.

Do not using anything stronger (e.g., super glue or gorilla glue).  It makes a mess, is too brittle, and is very hard to remove.  Hot glue is really the about perfect.

### "Feet" for Your Quadcopter

It's useful to have something for your quadcopter to stand on so it sits level on the ground.  This is especially handy when you are calibrating your IMU.   You have several options:

1.  You can use the motors.  Position them to ride low, so the bottom extends down a ways, and make sure you put them all at the same height.  The draw back is that wires can get banged around.
2.  3D print something.   Go crazy, but remember that weight is an issue.
3.  A piece of light foam would make a pretty good landing pad.  You can even use part of a household sponge.
4.  The battery can also help here if you mount it underneath.

### Attaching the Battery

The battery is awkward, and it's a hard problem to solve.  Many things can work, but few look great:  Blue tape, rubber bands, velcro.  

One thing that might help is shortening the wiring harness that connects to your quadcopter.  Play around until you find a good length and then trim it short.

We also have some plastic "cages" you're welcome to use.

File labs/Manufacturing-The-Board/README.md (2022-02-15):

# Tape out

To be completed in your groups.

Check the course schedule for due date(s).

## Skills to Learn

1. Prepare CAM files for submission to the manufacturer.

## Equipment, Supplies, and Software You will Need

1. Eagle
2. Your design review documents.
3. Your PCB schematic and layout.

## Tasks To Perform

### Finalizes your Design

This is your final chance to fix any problems. You should perform another design review yourself, after reviewing the checklist in the previous lab.

You should also be on the look out for any moments when a small voice in your head says “hmm… I’m not sure about that.” When that happens, ask about it on Piazza. Include a screen capture of the relevant parts of your board.

Follow the guidelines in the board layout lab under the heading "Generating Gerbers" to generate your final cam files.

### Commit Your Final Design

Commit your final design to your github repo. This should include

* Your updated `hardware/quadcopter.sch` and `hardware/quadcopter.brd`
* Your final `hardware/quadcopter.cam.zip`. Please be _certain_ that this the right cam files. I suggest deleting all cam files in your repo, regenerating them and zipping them up. Be sure to commit.
* A file called `hardware/metadata.txt` that has the following:

    1. Color you want your quadcopter to be. Choices are: Green, White, Blue, Black, Red, or Yellow.
    2. Silkscreen colors: White (if your board color is not white) or black (if your board color is white).
    3. The dimensions of your board in mm.

Submit it via Eaglint. You can expect the reviews to be quite stringent.

### The Ordering Process

**YOU DO NOT NEED TO ORDER YOUR BOARD. I WILL DO IT.**

This is just here for your information.

Some of you have asked about the ordering process.  We are using https://www.pcbcart.com/. To build the boards, you need to create an account, and then go to cart and “add item” to place an order.

Basically, you just upload the zip file of your cam files, and select some options, and pay with a credit card. Here are the options we will be using:

* 4 layers
* 5 boards (you’ll get 5 copies of your board)
* thickness 1.6mm
* color: based on your `metadata.txt`
* Surface finish: LeadFree ENIG
* Copper thickness: 1oz
* Gold fingers: no
* Material: FR4

A list of their capabilities is here: https://www.pcbcart.com/pcb-fab/standard-pcb.html. This is what get transcribed into the DRU file.

You can order a stencil as well (based on your `.crm` gerber).  However, I usually order stencils from https://www.oshstencils.com/.  They are smaller and a little easier to work with.

We have also had good results with https://jlcpcb.com/.

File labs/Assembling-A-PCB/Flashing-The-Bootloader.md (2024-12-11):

# Flashing the Bootloader and Bringing up Your Board

## You Will Need

1. Your board
2. A battery.
3. ISP Programmer
4. FTDI Board 
5. Multimeter
6. A computer with Arduino

## Electrical Short Test

By this time you should have received your PCB from manufacture and solder all the components to your board.  Before you power your board for the first time it is wise to check for shorts.  Use a multimeter to check for shorts between VBAT and GND and between 3.3V and GND.  Set the multimeter in continuity mode:
  
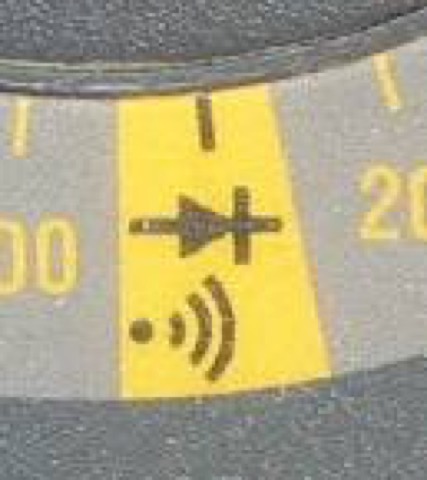
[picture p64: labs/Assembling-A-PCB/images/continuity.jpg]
Continuity test


Then apply the probes to the test points on or breakout headers.  If you hear a beep when touching a power net and a ground net, there is a short somewhere in your board and you need to fix it.  Talk to the TA or the instructor.
    
## Sanity Check (Device Signature Verification)

The in-system programmer (ISP) let's us program the microcontroller while it is installed on a PCB.  The first step is to connect the ISP programmer to the board.  Here's picture of the programmer:

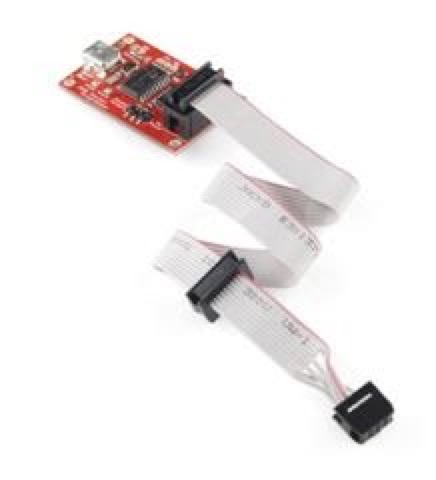
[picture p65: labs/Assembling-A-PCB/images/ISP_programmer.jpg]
AVR ISP Board


Attach a charged battery to your board, then connect the board to the AVR ISP programmer and the USB cable to your computer.  The 6-pin connector attaches the 6-pin header on your board.  The cable should point toward the three dashed lines on the side of the header:

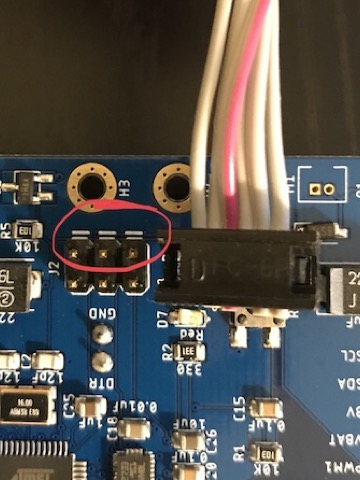
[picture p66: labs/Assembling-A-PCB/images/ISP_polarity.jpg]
ISP polarity


If the lights on the programmer go out, you have an electrical problem.  Look for solder bridges, then talk to the course staff.

The next step is to establish communication between your board and the ISP programmer. 

ISP polarity

First, check if your compute can communicate with the board.  For this (and the rest of the flashing process) we are going to use a command line tool called `avrdude`.  It can do tons of things to microcontrollers and is what Arduino uses internally.

Open your command line and type the following (it can take a few seconds to run):

```
avrdude -c usbtiny -p atmega128rfa1
```

If this doesn't work, check the following

* The `avrdude.exe binary` is in `Arduino/hardware/tools/avr/bin` on Windows and in `/usr/local/bin/avrdude` in MacOS.
  - You can add this path to your environmental variables paths so you can use this command in any directory in your shell.
* `avrdude.exe` asks for a `avrdude.conf` file. This file may be located in   `Arduino/hardware/tools/avr/etc`
  - You can copy averdude.conf to `Arduino/hardware/tools/avr/bin` or you can add the path to where you dowloaded `averdude.conf` like in the following command: `avrdude -c usbtiny -p atmega128rfa1 -C ~/Downloads/avrdude.conf`
* If avrdude doesn’t recognize the "Pocket AVR Programmer" you can find the drivers in the following website: https://learn.adafruit.com/usbtinyisp/download.

When it's finally successful, you'll see a message like in the following image should be displayed.

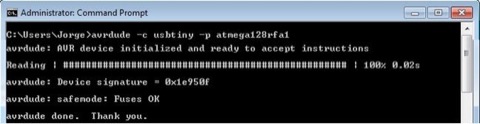
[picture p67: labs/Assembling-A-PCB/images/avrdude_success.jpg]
AVRDude Success


If the command displays an error (see images below) it means that the computer is not able to communicate to your board or that your computer couldn’t find the AVR ISP Programmer. Double check that your quadcopter switch is turned on if you see an "initialization failed" error.

AVRDude Error

The above error happens when your computer can’t find the AVR ISP Programmer. To solve this check that the device driver for the AVR ISP Programmer is installed.  If the tool suggests that your "override" with `-F`, don't bother.  It won't help.  Talk to the course staff.

For more information about how to use avrdude check this website: https://learn.sparkfun.com/tutorials/pocket-avr-programmer-hookup-guide 

## Flashing the bootloader

You are now ready to "flash" the bootloader.  This means we are going to write the bootloader into the non-volatile memory of the microcontroller.  The bootloader is a small program that allows us to reprogram the microcontroller over the serial port instead of the ISP header.
  
You’ll need the hex file that contains the bootloader.  It’s part of the `QuadClass-Atmega128RFA-Arduino-Addon` repo you intalled in Arduino during the first Arduino lab.  The file you need is `QuadClass_Atmega128RFA_Arduino_Addon/avr/bootloaders/ATmegaBOOT_atmega128rfa1.hex`

To flash the bootloader, run the following commands. The last one will fail, see below.

```
 cd <your quacopter repo>/firmware/hardware/QuadClass-Atmega128RFA-Arduino-Addon/avr/bootloaders/
 avrdude -p atmega128rfa1 -c usbtiny -e -U lfuse:w:0xff:m -U hfuse:w:0xda:m -Uefuse:w:0xf5:m lock:w:0x3F:m
 avrdude -p atmega128rfa1 -c usbtiny -B 1 -U flash:w:ATmegaBOOT_atmega128rfa1.hex -U lock:w:0x0f:m
```

The second command sets the fuses in the AVR microcontroller to configure the microcontroller to use an external clock, among other things.  The third command copies the `ATmegaBOOT_atmega128rfa1.hex` to the microcontroller.

The last command will fail due to a big in `avrdude`. You’ll see something like this:

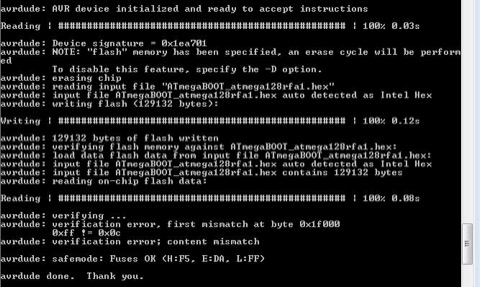
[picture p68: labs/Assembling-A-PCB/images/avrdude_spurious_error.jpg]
AVRDude Spurious Error


This is a known issue and is because the `USBTinyISP` protocol that we are using with the “[Pocket AVR Programmer](https://www.google.com/url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)" is incapable of addressing memory addresses in excess of 64 KB. In our case the atmega128RFA1 is of 128K.
“… Someone in the code put uint_16 for the address so it overflows…” (Ignore the error!)

## Programming The Board With Arduino

Open up the Arduino IDE and make sure it's configured properly (See notes in "Programmin The Hardware Lab").  The run the blink test on the board.  Your PCB should have a blinking light!  

Your board is not ready for use!

## Bringup

"Bringing up" a board means carefully checking that each component of the board works as expected.

There is a tendency to move to quickly during bringup, but take your time.  If you try to run a big piece of software at first, the bugs will be much harder to find.

### Bringing up the BBB

You should be able to the Arduino blinking light test.  You can also run `test_remote_harness.ino` on the BBB and `test_remote.ino` on your loaner remote.

### Bringing up the Remote

A purpose-built tester is useful here.  For instance, for the remote, there is `Quadcopter-Remote/src/test_remote/test_remote.ino` and `Quadcopter-Remote/src/test_remote/test_remote_harness.ino`.  `test_remote.ino` runs on the remote and transmits a bunch of data to another device (a working remote or a FCB) running `test_remote_harness.ino`.  It tests all the software-accessible components of the remote.
It doesn't, however, check that the battery charger works.  So, you'll need to verify that mannually.

### Bringing up Your Quadcopter

Your code from the first remote/FCB can also serve as a good starting point.  When bringing up your quadcopter, remember that the pin assignments may be differnt, so you may need to modify the code slightly.

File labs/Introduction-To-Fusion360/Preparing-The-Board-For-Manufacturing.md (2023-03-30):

# Part 3: Preparing the Board for Manufacturing

Once the design is finished, we need to translate it a format that the manufacturer can understand.

## Generating the CAM files

In order to have a board manufactured an Eagle or Fusion360 file is not sufficient. Instead, you need to produce a set of computer aided manufacturing (CAM) files for the design. Fusion360 provides a tool called the "CAM processor" to generate these files for your design. CAM files are also called "Gerber files."

Different board manufacturers (i.e., "board houses") require different types of CAM files and some require different CAM setups for different levels of board complexity. We will be using https://www.pcbcart.com/, a Chinese manufacturer that is pretty reliable and fast. Each board house and service level has different sets of restrictions the design must meet and, potentially, a different set of design files they require. Two files define how Fusion360 interacts with the board manufacturing process.

The first is the .cam file. This defines the set of gerber files we will send to the manufacturer. The second in the .dru file that defines the design rules for the board house. The specs for JLCPCB's PCBs are here: https://www.pcbcart.com/pcb-fab/standard-pcb.html. Fusion360 uses the design file to, for instance, guide the autorouter and perform sanity checks on our design.

The CAM file you need for this lab is in `Eagle/CAM/pcbcart-4layer.cam`.

<!--
To select the CAM file you will use, select "Window->Control Panel" Then select "File->Open->Cam Job..." and navigate to Eagle/CAM/jlcpcb-2layer-eagle9.cam.
You should see a window like this:
![](images/cam1.png)
Leave this window open and return to the board editor window.
-->

To select the CAM file, return to the board editor window, navigate to the `Manufacturing` tab and select the `CAM Processor`:

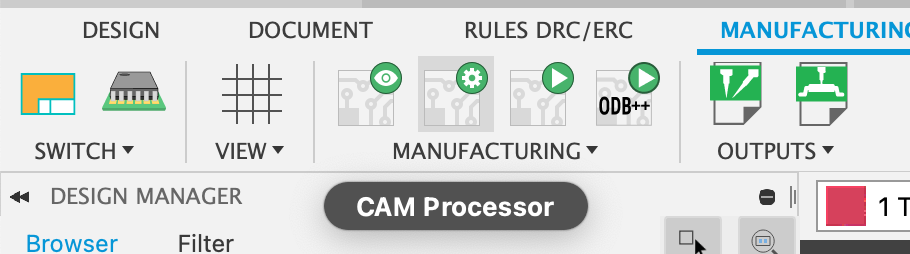
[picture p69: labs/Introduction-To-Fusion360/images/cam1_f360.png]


A window will appear like this:

<!--
the same window will reappear but with some additional information filled in:
-->

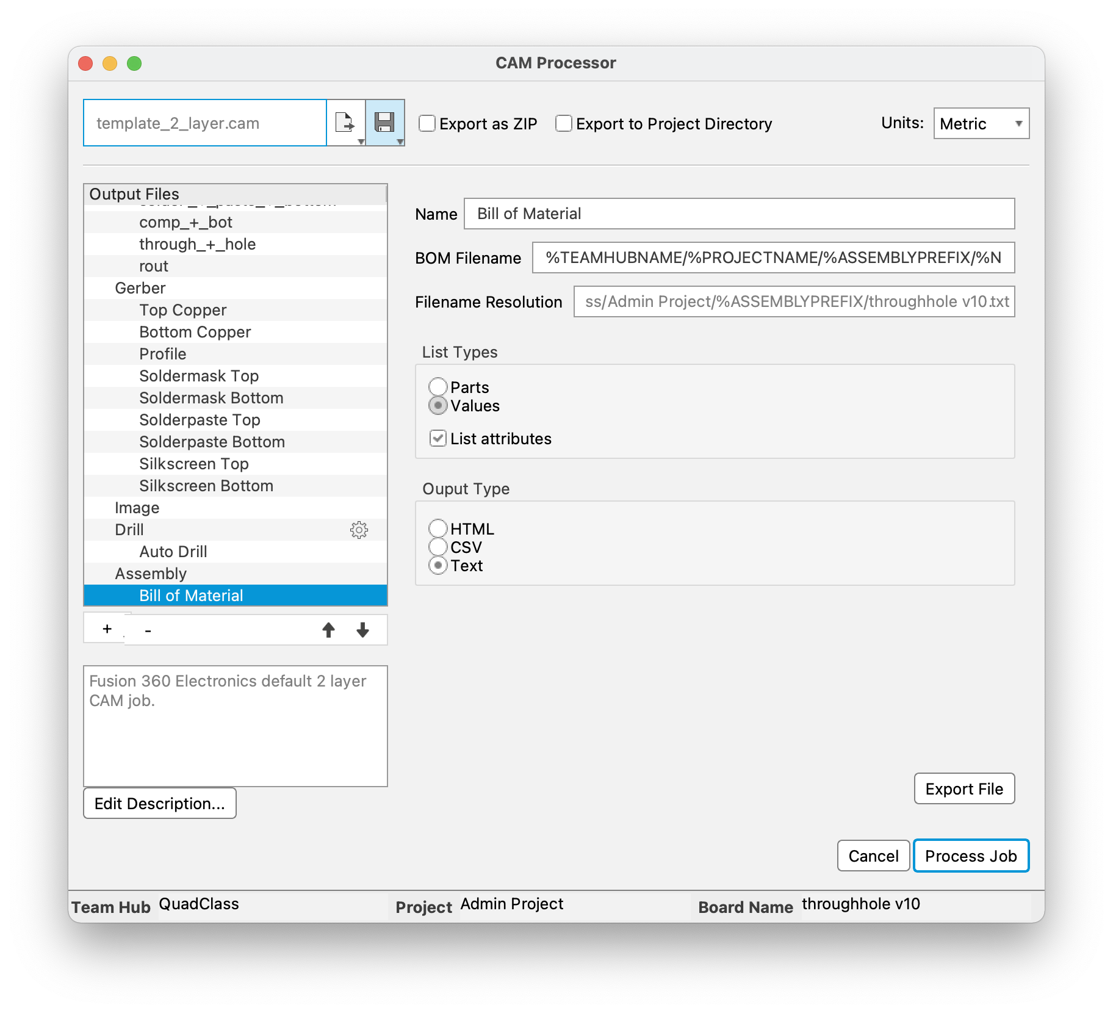
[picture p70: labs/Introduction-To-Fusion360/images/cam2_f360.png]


Then click on the "load job -> Open Cam File". This will allow you to select the required the CAM `Eagle/CAM/pcbcart-4layer.cam`. Keep in mind that this CAM is for a 4 layer PCB, while we are working on a 2 layer PCB, so you will see some warnings. However, this CAM file is needed for eaglelint which will automatically check your schematic and board files.

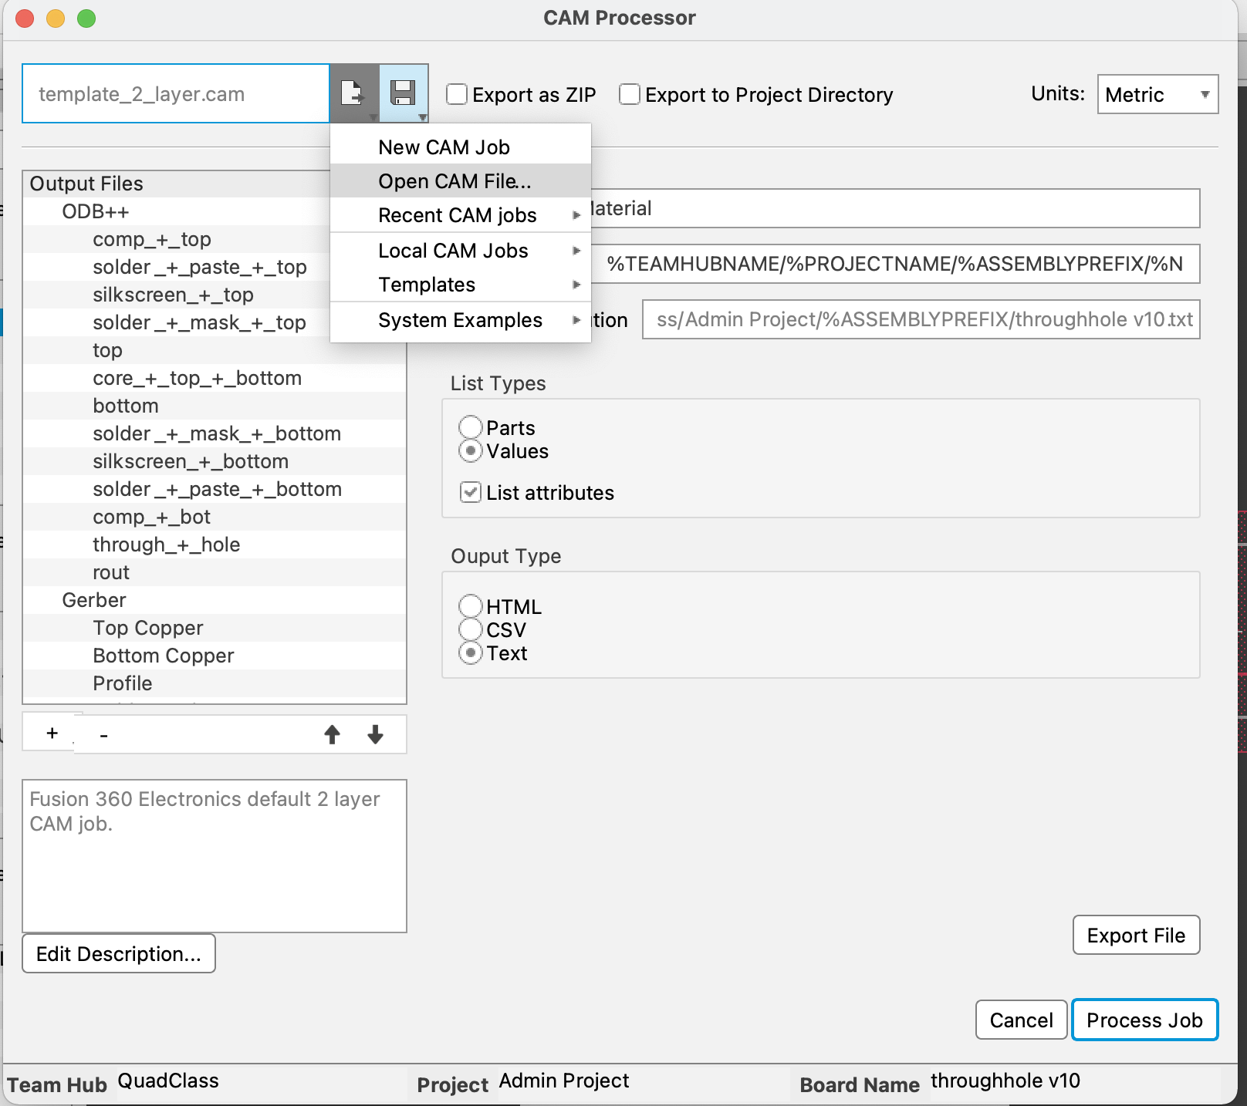
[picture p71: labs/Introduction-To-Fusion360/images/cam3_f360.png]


The tabs on the left correspond to the CAM files that the CAM processor will generate for this design. The body of the window contains configuration parameters for each of the CAM files. Don't touch any of these settings.

Click "Process Job". A progress bar will appear briefly and then vanish. The CAM files have been generated, and are saved wherever you specified.

Save the Gerber file as `throughhole.cam.zip`

## Viewing the CAM files

Fusion360 cannot open or view CAM/Gerber files. For that you need a Gerber viewer:

- Mac: I like Cuprum: http://www.wortum.com/cuprum/.
- Windows: http://www.viewplot.com/ or https://www.pentalogix.com/t/software-products/viewmate.
- Linux: http://gerbv.geda-project.org/ (It might already be installed. Or do `sudo apt-get install gerbv`)

The instructions below are for the Cuprum viewer on a Mac.

Launch Cuprum and create a new project (Command-N). Click "Import..." and then select all the files generated by the CAM file generator. These are:

- `throughhole.cmp`: This is the copper on the top layer of the board. You should see metal traces corresponding to the routed traces you added in Eagle. You should also see a circle at each pad.
- `throughhole.stc`: This is the solder mask for the top of the board. Solder mask is the green material that covers the surface of the board. It protects the metal from corrosion and accidental electrical connections. This layer is a negative. It shows holes that will appear in the solder mask, exposing the parts of the copper that we need to make connections to. There should be a circle around each of the pads.
- `throughhole.plc`: The silkscreen layer contains the write documentation and markings that appear on the surface of the board. It should contain the outlines of the parts and their reference designators (e.g., "LED1").
- `throughhole.sol:` Bottom metal layer.
- `throughhole.sts`: Just like `stc`, but for the bottom of the board.
- `throughhole.pls`: Just like `plc', but for the bottom of the board.
- `throughhole.ncd`: This is the drill file. It determines where holes will be drilled in the board. There is one hole for each of the pads in our design. There would also be pads for Vias and “mechanical holes” for mounting etc. Unfortunately, the format the Seeed requires for the drill file does not display well in the gerber viewer, so the holes will be all over the place.

Load them, and then examine each by toggling its visibility in the viewer:

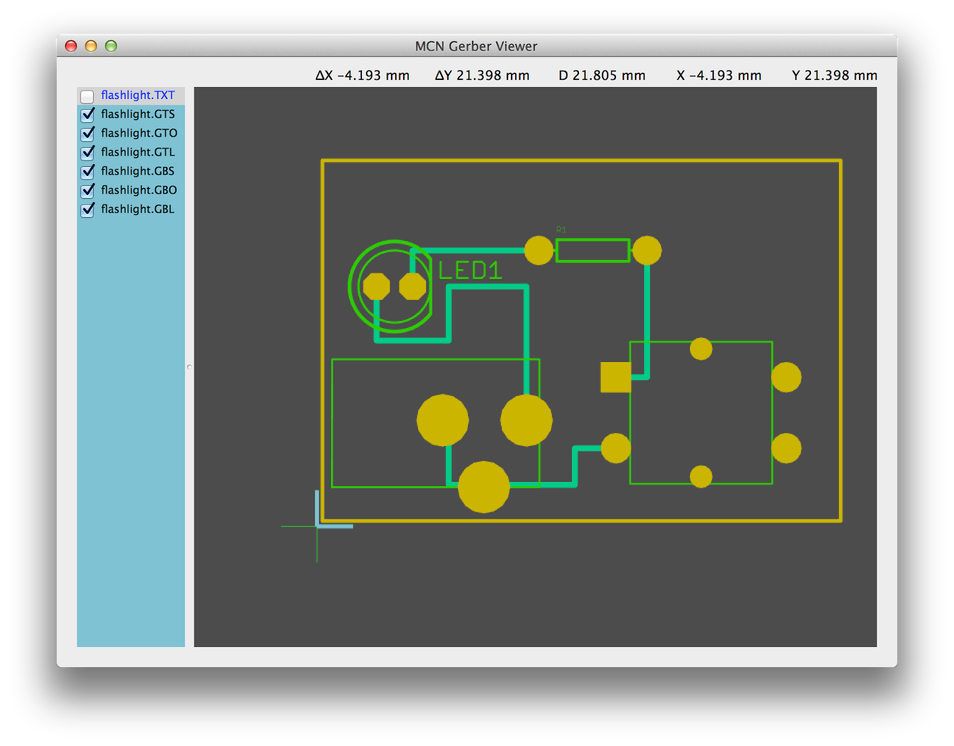
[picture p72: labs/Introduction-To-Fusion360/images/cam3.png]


3. Make sure the File name matches the File Content. You will probably need to change the File Content for the *.drd to *NC Drill.\*

After you've verified that the CAM files look good, you're ready for [part 4](Creating-Surface-Mount-Parts.md)!

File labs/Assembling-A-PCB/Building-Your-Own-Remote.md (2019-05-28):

# Building Your Own Remote

The base model of the remote is what we have in class.  There are several options you can add.

## Electrical Components

You'll need to order the parts that are required for the remote but not for the breakout board.  To do so:

1.  Go to https://www.digikey.com/ordering/shoppingcart?lang=en
2.  Click `Upload a File` select [remote.digikey-bom.csv](boms/remote.digikey-bom.csv).
3.  Column B is the Digikey part number.  Column C is the quantity.  Ordering 1 spare of everything is not a bad idea. 
4.  Complete you order.

## Mechanical Components

Items with a "*" I can provide, since I buy them in bulk.

| Desc |  URL | Qty | 
|---|---|-----|
| FTDI cable |  https://www.adafruit.com/product/206 | 1 | 
| USB Micro cable  |  You probably have one of these | 1 |
| Display | https://www.sparkfun.com/products/14072 |  1  |
| LCD mount screws	1 1/4 in | 	https://www.mcmaster.com/90272a087 | 4 *| 
| Gimbal screws	1 1/2 in |	https://www.mcmaster.com/90272a088 | 8 *|
| Nuts for gimbals and PCB	|	https://www.mcmaster.com/90480a003 | 12 *| 
| Servo cable 	| https://www.amazon.com/gp/product/B01J81HQ9Y | 2 *|
| 3/8" spacer | https://www.mcmaster.com/94639a709 | 4 * |
| 1/2" spacer | https://www.mcmaster.com/94639a713 | 4 * |
| 1" spacer |  https://www.mcmaster.com/94639a667 | 8 * |
| Battery cable | https://www.alibaba.com/product-detail/Wholesales-explosion-proof-2-pin-Molex_60813679908.html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 | 1 *|
| Baseplate | na | 1 * |

## Gimbals

These are a little harder.  They are frequently out of stock.  They are also different than the ones on the remote I loaned you.  Unfortunately, those gimblas have been discontinuned.

| Desc | URL | Qty | 
|---|-----|-----|
|Gimbal (L) |https://hobbyking.com/en_us/turnigy-9x-9ch-transmitter-replacement-throttle-rudder-gimbal-1pc.html|	hobbyking|
|Gimbal (R) |https://hobbyking.com/en_us/turnigy-9x-9ch-transmitter-replacement-elevator-aileron-gimbal-1pc.html|	hobbyking|

## Assembling the Display

The remote includes a female header on the board that connects to a male header on the display.  Soldering the headers so they align is tricky, but there's a trick:

Barely insert the male header into the female header and the attach the display to the remote board using the screws.  You'll need 4 donuts between the LCD and the remote board.
 
Position the headers (without soldering them) so the male header connects to the display, and the female header connects to the remote.  Gently squeeze the two boards together and scew in place.

The headers are now perfectly positioned for soldering.  Solder them to the display and the board.

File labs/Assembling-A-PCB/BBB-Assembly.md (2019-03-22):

# Bare Bones Board Assembly Drawings

Below are the assembly drawings for the BBB.  For each part, the locations of the parts on the board are highlighted.

## 10KOhm Resistors

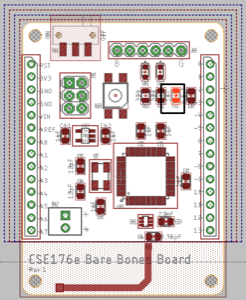
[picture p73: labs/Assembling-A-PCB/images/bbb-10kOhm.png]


## 330Ohm Resistors

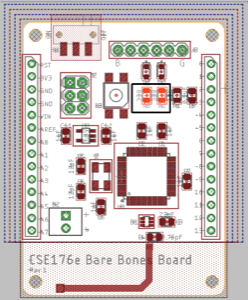
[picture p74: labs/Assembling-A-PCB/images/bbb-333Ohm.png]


## 0.75 pF Caps



## 12 pF Caps



## 1 uF Caps



## 22 pF Caps



## Voltage Regulator



## Button



## Crystal



## LEDs



## Power Switch



## Balun



## Microcontroller



## FTDI Header



## SPI Header



## Battery Terminal



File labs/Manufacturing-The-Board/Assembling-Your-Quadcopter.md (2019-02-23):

# Part 2: Quadcopter HW debugging and Motors rotation

## 

## Debugging your quadcopter hardware
Before moving to MultiWii is highly recommendable to test the hardware in your quadcopter and see if everything works.

* *Testing IMU:*

    * Some of your designs have the low-order bit of the IMU I2C address set incorrectly. You can change the values the library uses by changing `LSM9DS1_ADDRESS_ACCELGYRO` in `Adafruit_LSM9DS1.h`. For some of you the IMU seems to be reporting the wrong ID as well. You can disable this check in `Adafruit_LSM9DS1.cpp` look for `LSM9DS1_XG_ID`. You’ll probably need to disable the check on `LSM9DS1_MAG_ID` too.

* *Testing Antenna:*
* You can use the code you did for Lab1 or you can move on to Multiwii, install the code and test it with the controller.
* *Testing LEDs:*

    * Make a code for turning on and off the LEDS.

* *Testing* *Motors:*

    * Make a code for testing the motors.

Just for the reference here are the pinouts of the ATmega128RFA1 chip and the numbers in Arduino.

[image:https://lh3.googleusercontent.com/Y-g-L73snOodRgEldgMqoe6ZkE8HG2E9gaV6Dzdi6jYx83d-sB-QP6XNzDjoGwq-7iR392esXOIleYe5_OIb4UZCEGeV_r1Y0PgZhrV2A9kyVv5TjLU=w371]

## 

## Connecting the Motors
The proper way of connecting is the following:

[image:https://lh6.googleusercontent.com/Udl2DeEpNyP6dQ8fEz-RLj-oiEe32Y_gbZe2rgo36ftyuY-uYHG6NjrNH1-W-WyVhS_R_edBquHyBHo3qT8ogQRrjCrvrM5WJWKGY6VzKYvwgfqC9HY=w673]

Depending on your Quadcopter configuration (Quad + or Quad X) connect the motors so that the above picture match.

Check your schematic to figure out which pin of the connector is the positive and which one is negative.

[image:https://lh6.googleusercontent.com/5aGaMqNbBq0CTBH3FEu3-_WgT2El_n9up7iqOvvy34DylCeBS4ww7qkAEeE8xfh9YAnAo2nQiIxwplMkVLGj-BiH08DTkNwuzSFGxCnuPnhBGH9O2TY=w170]

If you switch the polarity of the cables your motor is going to spin in the opposite direction and contrary to the brush inside the motor therefore reducing the life of the motor. That is why there exists two types of motors (CW and CCW).

## 

## Propellers
There are two types of propellers (CW and CCW). When inserting the propellers to the motors just make sure that the motors trow air to down and not up. Also propellers can come in different colors, is common to place different colors at the front and back of your quadcopter to know the orientation when it is flying.

[image:https://lh4.googleusercontent.com/m_oq1LI_hATVSxeVcqnpruCNJ5CESinBkgc32T9WAJ6Aa5gUfhQjtpXtC_OJOs0j954Ys0B-ZLXjJV_FZHb7IjceEdLDrKEXaQAISViopxvt4Z-G0Hg=w673]

# Part 3: Flight Control

## 

## Tasks to Perform (Part Lab06c): Flight Control Features
### 

### Implement Control Features
You need to implement the following features in your quadcopter firmware

Arm

When you power up your quadcopter it should be “disarmed.” This means that it will not respond to the remote. This is safety feature (to prevent the props from running unexpectedly) and an opportunity to calibrate your sensors.

A common way to arm a quadcopter is to hold the throttle at zero and the roll gimbal all the way to one side or the other and wait a few seconds. You can use whatever method you like, but it must include the throttle being at zero.

It’d be nice to indicate when the quad is armed by flashing a light or something.

Calibrate your IMU

When the quadcopter boots, it should calibrate the IMU. You should assume that the quadcopter is sitting on something level and check the measurements from the IMU to account for any offsets. Your quadcopter should refuse to arm itself until it’s calibrated.

It’d be nice to have a light that shows when it’s calibrating and/or when it’s ready to be armed.

## 

## Complete The Flight Controller
The code you wrote for the test stand should be more or less ready to run on your quadcopter. In theory, the only changes you should need to make to get flying (but maybe not steering) are to update the pin assignments for your motors, re-tune the PID values, and add a PID channel for roll (assuming you were working on pitch on the test stand). For full flight control you’ll need to add a PID channel for and yaw.

### 

### Tuning the PID Values
The process is same as it was for the test stand, with a few small changes.

1. Your quadcopter probably has more power than your test stand because the power delivery system is cleaner (your nice big power/ground planes are much better than the skinny wires on the test stand)
2. The mass and balance of your quadcopter is different than the test stand.
Both of these mean that the correct PID values for your quad are probably different than those for the test stand.

You can tune the values by attaching your quadcopter to the test stand. To do this, you can pull the pivot platform off the axel and attach your quad using tape or zip ties (available in the maker studio).

### 

### Adding the Roll PID Channel
The PID control for roll works the same as for pitch. In theory, if your quad is symmetric the PID values should be the same too. I would check by rotating the quad on the test stand and seeing how stable it is.

Once you have the roll channel added, your quadcopter should be able to fly — i.e., you should be able to increase the throttle and it should leave the ground and fly level. However, it may spin because you don’t have yaw control yet.

For your quad’s safety, you may want to attach the prop-guards that came in your crash kit. The prop-guards make it less likely that the props will cut someone and they also help prevent damage to the motor shafts — a hard crash on a prop can bend the shaft and ruin one of your motors.

These are the loopy piece of black plastic. It has four mounting points that attach the motors, but the dimensions won’t quite match your quad. You can cut it into four pieces and attach a piece to each motor.

### 

### Adding the Yaw PID Channel
The Yaw channel is a little different. Use the left-right axis of the left controller gimbal to set the rate of rotation. This is exactly what the gyro gives you. The gyro is also pretty low noise, so you probably won’t need to do much filtering.

Tuning this PID loop is harder, since the test stand doesn’t spin. However, yaw is also not as critical for stable flight so you can probably tune it while the quadcopter is in the air.

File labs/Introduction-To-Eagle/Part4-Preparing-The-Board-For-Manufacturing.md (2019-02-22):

# Part 3: Preparing the Board for Manufacturing

Once the design is finished, we need to translate it a format that the manufacturer can understand.

## 

## Generating the CAM files
In order to have a board manufactured an Eagle file is not sufficient. Instead, you need to produce a set of computer aided manufacturing (CAM) files for the design. Eagle provides a tool called the "CAM processor" to generate these files for your design. CAM files are also called "Gerber files."

Different board manufacturers (i.e., "board houses") require different types of CAM files and some require different CAM setups for different levels of board complexity. We will be using [JLCPCB](https://www.google.com/url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), a Chinese manufacturer that is pretty reliable and fast. Each board house and service level has different sets of restrictions the design must meet and, potentially, a different set of design files they require. Two files define how Eagle interacts with the board manufacturing process.

The first is the .cam file. This defines the set of gerber files we will send to the manufacturer. The second in the .dru file that defines the design rules for the board house. The specs for JLCPCB's PCBs are here: [https://jlcpcb.com/capabilities/Capabilities](https://www.google.com/url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). Eagle uses the design file to, for instance, guide the autorouter and perform sanity checks on our design.

The DRU and CAM files you need for this lab are in `Eagle/CAM/jlcpcb-2layer-eagle9.cam` and `Eagle/CAM/jlcpcb-4layer-eagle9.cam`.

To select the CAM file you will use, select "Window->Control Panel" Then select "File->Open->Cam Job..." and navigate to Eagle/CAM/jlcpcb-2layer-eagle9.cam.

You should see a window like this:

[image:https://lh4.googleusercontent.com/UaL8NLWIti2GAHe6Ut47vF38owBsj8eIvICQfvICN_keAhxPIMmqCvvbyBzsIHI16JdYs4yMYMP50ndshUzUBZKyogimw0uo5IZlEpfNp_SqvJ1jCw=w1175]

Leave this window open and return to the board editor window. Select "File->CAM Processor..." the same window will reappear but with some additional information filled in:

[image:https://lh4.googleusercontent.com/xxHMhgvj4U9iXDD8WepCBi7nSduyoOMjRCUqeW9JABAUL9IHP9XNm8VHcCP44hUGMvAb8MKUquGI4SG0DgNsj1Vns89pQhKwYy3xLuEJcv6xPkAa5A=w1175]

The tabs across the top correspond to the CAM files that the CAM processor will generate for this design. The body of the window contains configuration parameters for each of the CAM files. Don't touch any of these settings.

Click "Process Job". A progress bar will appear briefly and then vanish. The CAM files have been generated, and are now in the same directory as your schematic and board files.

## 

## Viewing the CAM files
Eagle cannot open or view CAM/Gerber files. For that you need a Gerber viewer:

* Mac: I like Cuprum: [http://www.wortum.com/cuprum/](http://www.google.com/url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).
* Windows: [http://www.viewplot.com/](http://www.google.com/url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)
* Linux: You'll need to find one. Let me know if you find a good one.
The instructions below are for the Cuprum viewer on a Mac.

Launch Cuprum and create a new project (Command-N). Click "Import..." and then select all the files generated by the CAM file generator. These are:

* *throughhole.TOP*: This is the copper on the top layer of the board. You should see metal traces corresponding to the routed traces you added in Eagle. You should also see a circle at each pad.
* *throughhole.STC*: This is the solder mask for the top of the board. Solder mask is the green material that covers the surface of the board. It protects the metal from corrosion and accidental electrical connections. This layer is a negative. It shows holes that will appear in the solder mask, exposing the parts of the copper that we need to make connections to. There should be a circle around each of the pads.
* *throughhole.PLC*: The silkscreen layer contains the write documentation and markings that appear on the surface of the board. It should contain the outlines of the parts and their reference designators (e.g., "LED1").
* *throughhole.BOT:* Bottom metal layer.
* *throughhole.STS*: Just like GTS, but for the bottom of the board.
* *throughhole.PLS*: Just like GTO, but for the bottom of the board.
* *throughhole.*: This is the drill file. It determines where holes will be drilled in the board. There is one hole for each of the pads in our design. There would also be pads for Vias and “mechanical holes” for mounting etc. Unfortunately, the format the Seeed requires for the drill file does not display well in the gerber viewer, so the holes will be all over the place.
Load them, and then examine each by toggling its visibility in the viewer:

[image:https://lh3.googleusercontent.com/u5XrCIwk0Ox7ZiVD1FMtRbzrv62q54DOgYZZeoq64mErTKeGJIS_LgSyk2q6sGFiWLkfHN6EupbB1AjJzZxIFBy5IYClDDOkeRpCfo1P3R_7_01ynlg=w1175]

3. Make sure the File name matches the File Content. You will probably need to change the File Content for the *.drd to *NC Drill.*

4. Below this page there are some options that you need to fill. The following ones are required.

Company Name: [UCSD or Any]

Phone: [Any Phone]

First Name: [Any Name]

Last Name: [Any Name]

Email: [Your email]

Part Number: [Any Number]

Revision #: [Revision number of your board, 0, 1, 2, etc.]

Layer Count: *2*

X Dimension: [X Dimension of your board in inches]

Y Dimension: [Y Dimension of your board in inches]

Silk Screen Sides: *Both Sides*

ITAR: *No*

If you don’t know the dimensions of your board you can use the eagle tool called “Dimensions”. Place this tool over the X and Y dimensions of your board and the measures will appear.

[image:https://lh4.googleusercontent.com/rogIVtRYArZwZlMBmvDYtFYRrFXD27wUS2H0_tozJQGmyi_7eBWnC7erehjpOyOMMfb09CjfWDR6nKPpQU0WUdhS0ETk0ycoxFEaXw214KD7rEdx9lc=w673]

Be careful, remember that you need the measures in inches. You can check or change the measures to inches using the “Info” tool and then select the number that is shown in the measures for the X and Y dimensions you got.

[image:https://lh4.googleusercontent.com/z6U0gkP9xUB--DOJihBGjNjWmHjkZDgBzu7tuQzh_kBEeVU4ha5T1reFgThAbVUxYFcPkYE-LLbpstT1-jMGHgr5_UMuxbHzQVtOJpXk7f4C0bjT_sZL=w673]

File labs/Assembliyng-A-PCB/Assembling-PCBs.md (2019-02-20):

# Assembling PCBs

folds over to the right.  Keep that space clear
Tools on the left
Put stencil in "portrait" orientation
clean up stencil with alcohol

## Preparation

Assembling a board (especially your first one) can take a couple hours.  Also, the working time for the solder paste is limited, so you need to work reasonably quickly once you start.

Begin by making sure you have everything you need. 

## Applying Solder Paste

### What You Need

1. Blue tape
2. Solder stencil
3. 4 scrap PCBs the same thickness as your board. 
4. 1 large putty knife
5. 1 small putty knife
6. Butcher paper
7. Gloves
8. A magnifier
9. Alcohol in a pump dispenser
10. Kimwipes
11. Compressed air
12. Solder paste

### Preparing Your Space and Aligning Your Stencil

You need a large, clear space to apply solder paste.

1. It can be messy, so cover everything with butcher paper.
2. Tape down your scrap PCBs so they will hold your board still.  The PCB should be oriented so the stencil aligns with it in "portrait" orienation (tall rather than wide).
3. Align your stencil with your board so the wholes line up perfectly with the pads. This must be very precise.
4. Tape down the right edge of your stencil so you can easily lift it on and off your board like a page of a book.
5. Check the alignment again
6. Verify your alignment with course staff.

### Apply Paste

1. Use the narrow putty knife to apply a thin (1cm) bead of paste to the edge of the wide putty knife.
2. Hold the wide putty knife at a 45-degree angle and drag it across the stencil, forcing the paste through the holes.  Press pretty hard and move smoothly.  Make sure you align the knife so it will pass over all the pads on the board.  You can only make one pass. 
3. Carefully and gently and in one motion, lift up the stencil and fold it back.
4. Examine the paste pattern with your magnifier.  Look out for
   * Pads with missing paste
   * indistict or touching paste blobs (esp. on the IMU and microcontrollers)
5. Check it with course staff and point out any problems you spotted.
6. If it looks good, carefully remove your board.
7. If something is wrong, you'll need to remove all the paste using chemwipes and alcohol and start again.

### Cleanup

1. If someone else is going to use putty knifes immediately, you can leave them.
2. If not (or in doubt), clean them my scraping the paste back into its container and wiping them with alchol and chemwipes.
3. Wipe up any stray solder paste on the table, *both* sides of the stencil.
4. Blow any remaining solder paste out of the stencil holes with compressed air.

## Placing Components

### What You'll Need

1. A complete part kit for your board.
2. A pair of tweezers
3. A magnifier.
4. Steady hands.

### Get Organized

You need to place parts carefully and precisely.  You also need to work somewhat quickly.  With practice, you can place a board like the remote or the FCB in 10 minutes.  You should not take more than an hour.  Getting organized will help you meet this goal.

1. Get _everything_ you need together at once.
2. Have a clean work area (preferably with a white surface).  The parts are _tiny_.  The less stuff there is around, the less likely you are to lose anything.
3. Make sure there are no strong winds blowing (drafts, open doors)
4. Make sure you are unlikely to be bumped.
5. Allow adequate time.  
    * Paste has a limited working time, and the course staff are not around forever.    
    * Assembly will take ~1 hour.  Reflowing takes ~12 minutes.  Something will go wrong, budget ~30min.  
    * So, you shouldn't start assembly unless you have _at least_ 1:45 left in class.
5. Eat something before hand.

### Tips

1.  Dump out all the parts of a particular type on your work surface.
2.  Once the part is down, don't fiddle.  Moving the parts smears the paste.  The parts will self-align a bit during reflow, so it doesn't have to be perfect.
3.  If a part is upside-down, picking it up and dropping it is a good (if probablistc) way to turn it over.
4.  Don't pick up the board.  You more likely to bump a part if you pick up the board.
5.  Arrange your pile of parts at your board so you don't have to reach over the board, otherwise, you're more likely to bump parts.
6.  Don't mess up.  If something goes significantly wrong, you have to start again.
7.  Do one type of part at a time (e.g., 100Ohm resistors).  You have exactly the right number of them, so when they are gone, you're done.
8.  Typing `show C1 C2 C3` in Eagle will highlight where `C1`, `C2`, and `C3` are on the board. 
9.  You are to almost drop the parts onto the board.  Do not press them down.  It'll displace the solder paste.
10.  If you think you've messed things up, get the TA or prof.  They may be able to save you...or not.

### Notes Particular Parts

I suggest you proceed in this order.  This is roughly from easiest to hardest.

Note that on the remote, there are many parts you will leave unpopulated. Only put parts where there is solder paste.   

#### Resistors

1. These are pretty easy -- a good warm-up.
2. Make sure they are marking-side-up.

#### Capacitors

1.  The small caps are non-polarized, so direction doesn't matter.
2.  The big caps are polarized. The stripe goes near the dot. (Quad/FCB only)
3.  Align these carefully.  If you get it wrong your board will look ugly.

#### MOSFETs (Quad/FCB Only)

1. The correct orientation is obvious.
2. You need to align the pins carefully.

#### Voltage Regulator and Battery Charger.

1. Orientation is obvious (there's three pins on one side and 2 on the other)
2. Be sure not to confuse these two if you are assembly a remote.
3. Only the remote has a charger.

#### Button 

1. Either orientation is ok.

#### Crystal

1.  It seems like orientation should be important, but it's not.  The part is diagonally symetric. 

#### LEDs

1. This is your first polarized component, pay close attention or your board will be doomed to darkness.
2. The green line (yes, there really is one) goes near the dot. 

#### Diodes

1. These are also polarized, but the markings are extremely hard to see.  They are printed black on black.
2. If you hold the diode and look at in the light, one end has a faint rectangular bar code on it.  The other has an "S"
3. The barcode goes near the dot.

#### Balun

1.  The red dot faces up and goes next to the dot.  This means the red dot will be farther from the microcontroller and nearer the antenna.
2.  Pay close attention to the aligment.
3.  Check it with your magnifier.

#### Microcontroller

1.  Make sure you orient it correctly.  The dot goes next to the dot.
2.  The silkscreen markings fit tightly to the corners of the package, so use them as a guide. 
3.  Once it's down, check the alignment.  If it's not perfect, do not pick it up.  Instead, nudge it every so gently to align it.
4.  The magnifier will help you check alignment.  You can see the pads on the side of the package.  the need to be aligned with the patches of solder paste on the board.

#### IMU

1.  Similar to the microcontroller.
2.  The dot goes near the dot.
3.  Use the silkscreen markers to align it and the "drop" it on.
4.  The pads are smaller, so alignment is more important.
5.  Don't fiddle!

#### 6-pin Header (Remote Only)

1.  Not hard, but it sticks up and is easy to bump, so do it last.

#### USB Recipcal (Remote Only)

1.  The key point of alignment are the pins on the back and 5 pads on the board.
2.  Check it with the magnifier.

## Reflow

### What You Need

1. A TA or professor.
2. The reflow oven.

## Touch Up and Throughole Components

### What You Need

1. Soldering station.
2. A syringe of flux.
3. Thin, lead-free solder.
4. Swaps and/or a horse-hair brush.
5. Alcohol in a squirt bottle.
6. kimwipes.
7. Blue tape.

### Cleaning up Flux Residue

Wire solder has flux in the middle to help the solder flow.  SMD rework requires adding flux manually.  In either case, the result is a yellow-brown, unattractive residue that starts out sticky and hardens over time.

To keep your board looking nice and clean, you should remove it ASAP.  If you have several things to fix, do not wait till the end.  Due it one part at a time.  To clean up the flux, place a kimwipe over the area and squirt rubbing alcohol onto it.  Then, take a hair brush of swap and rub the kimwipe around over the area.  It'll absorb the flux residue.  Repeat once or twice.

If you don't have alcohol in a squirt bottle, just get the kimwipe very moist with alcohol and put it on mannually.

### Mounting Throughhole Parts

#### Headers

1.  Tape down the power jumper, debug header, FTDI header, and gimbal pins (remote only) using blue tape. 
2.  The main challenge is getting them straight up and down and not crooked.  Do your best.
3.  The white gimbal sockets go on top.  The 6-pin header connectors go on the bottom. (Remote only)

#### Battery Terminals

1.  Similar to the headers, but orientation matters.  The holes on the side should point toward the '+' and '-' on the board.

#### Motor Recepticals (Quadcopter only)

1.  Orientation is very important.  Removing/replacing these things is really hard. 
2.  The pins are not centered, and part should be oriented so it fits completely inside the silkscreen outline.  If it's backwards it'll protrude on one side.

### Common Reflow Problems

You should inspect all the parts on your board for problems.  

1. Sometimes solder won't reflow on some parts of the board.  You can tell because the solder paste is rough and not shiny.  To fix it, add a _tiny_ amount of flux and touch it with your soldering iron.
2. Parts sometimes get dislodged during reflow (It's actually pretty windy in the oven).  If only one terminal of the device is still connected, melt that side and lift it up.  If two terminal are connected, see course staff.
3.  You realize you forgot a part.  See course staff for a lesson in mannual surface mount assembly.

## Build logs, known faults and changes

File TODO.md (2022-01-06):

## Future Updates for Fusion360

1.  Update Lib01.lbr and associated parts to have 3D models.
2.  In the future remember to give them Lab01 in the cloud to start with.

## Preclass Tasks

1.  The assembly labs requires us to provide students with part kits.  To do this we provide labeled, pre-cut portions of 
part tapes.  We need part portions for both the practice assembly lab and the quad assembly lab.
2.  Practice assembling a BBB, a FCB, and a remote.  Learn the following:
    1.  How to set up paste station
    2.  How to apply paste
    3.  How to reflow
    4.  How to rework
    5.  How to bring up
3.  Become familiar with part organization.
4.  Run something through eaglint.
5.  Do the first lab.

folds over to the right.  Keep that space clear
Tools on the left
Put stencil in "portrait" orientation
clean up stencil with alcohol

assembly equipment

blue tape
tweezers
putty knives
alcohol
chem wipes
butcher paper
gloves
scissors
spray adhesive
magnifire
compressed air

Soldering equipment

blue tape
alcohol
brushes
swabs
solder
flux
chemwipes

TA Tasks

8. Do Lab 1 and update the screen caps.
9. Do Lab 1 and check that git@github.com:NVSL/QuadClass-Eagle-Intro-Solution.git is a solution that matches the lab.  In particular, cam generation has changed significantly.  Have them commit a zip file of their cam file.  Run the solution to eaglint to make sure. 
2. Make labels for each component type with space to write qty.
3. Prepare part strips for BBB assembly.
6. Collect all the data sheets for quadparts_prebuilt.lbr.  Put them in the resources repo.
10. Dismantle old remotes
0. Build a remote
1. Build an FCB

Tasks

1.  Set student count
1.  Laser cut remote 
2.  Laser cut test stands.
2.  Order lots of stuff
3.  Move layer label part into quadparts_prebuilt.  Require it's presence in the design.
5.  Remember to handout research release form at the beginning of class.
6.  include major, year, etc. and demographics on both the pre-survey and the post-survey
7.  Ask the "can you do X" questions on the presurvey.
8.  Do a survey on the first day, and another in two weeks to see who you lost.
9.  Label stencils
10.  

Next Time:

Generate unified BOM:

python ../../Eagle-Lint//server/eaglint/BOM.py --sch controller_board_cheap.sch ../../QuadClass-Quadcopter-Solution/flight_control_board.sch --format csv --out controller_board_cheap.digikey-bom.csv --qty 45 30 --extra 0.2

## Future Years

1. Eliminate the bridge and draw the ground plane to make the ground return from the voltage regulator clean. 
2. Replace the vreg on the remote with a combined charger/LDO. 
3.  Integrate skill inventory into application.  It might help tell whether I could offer this to juniors

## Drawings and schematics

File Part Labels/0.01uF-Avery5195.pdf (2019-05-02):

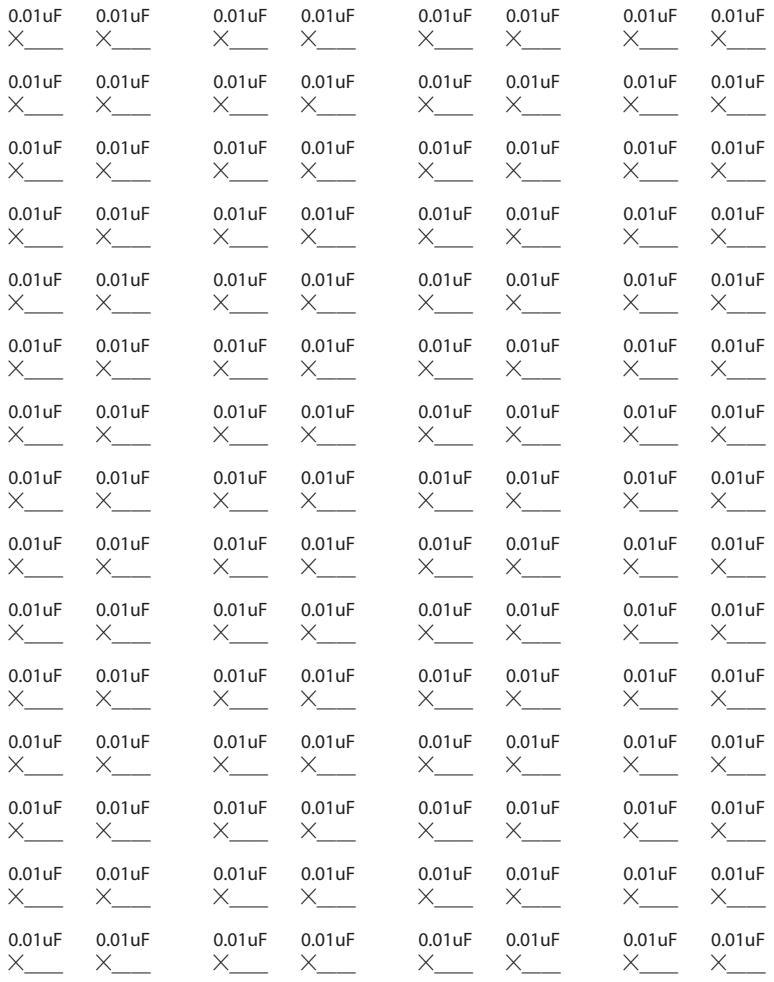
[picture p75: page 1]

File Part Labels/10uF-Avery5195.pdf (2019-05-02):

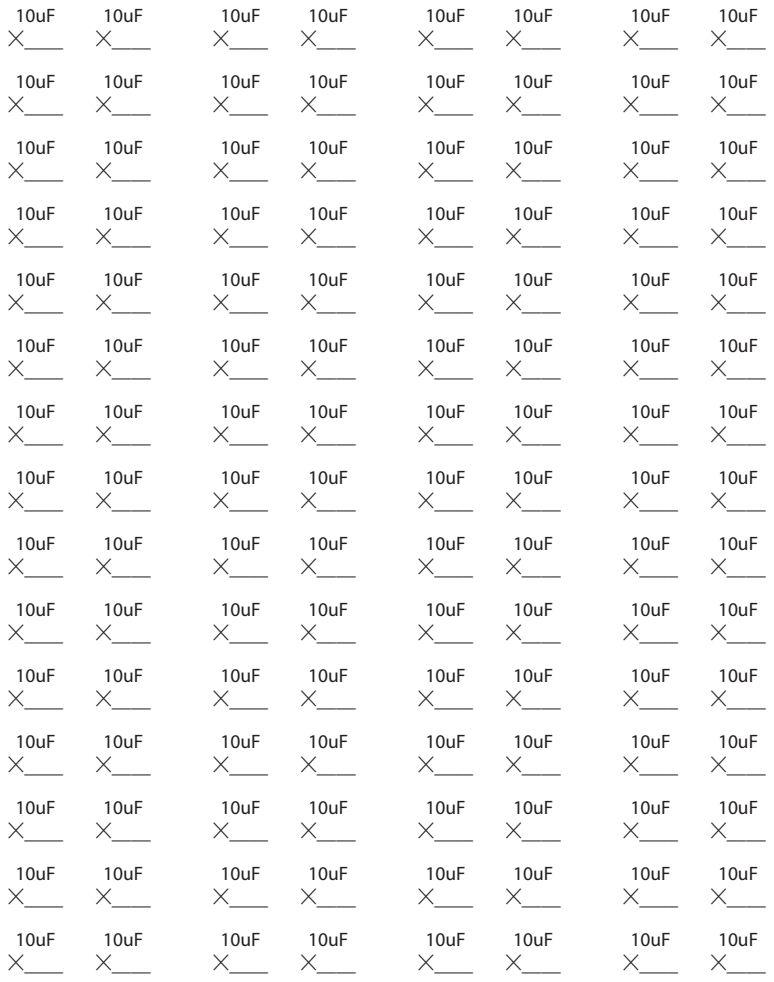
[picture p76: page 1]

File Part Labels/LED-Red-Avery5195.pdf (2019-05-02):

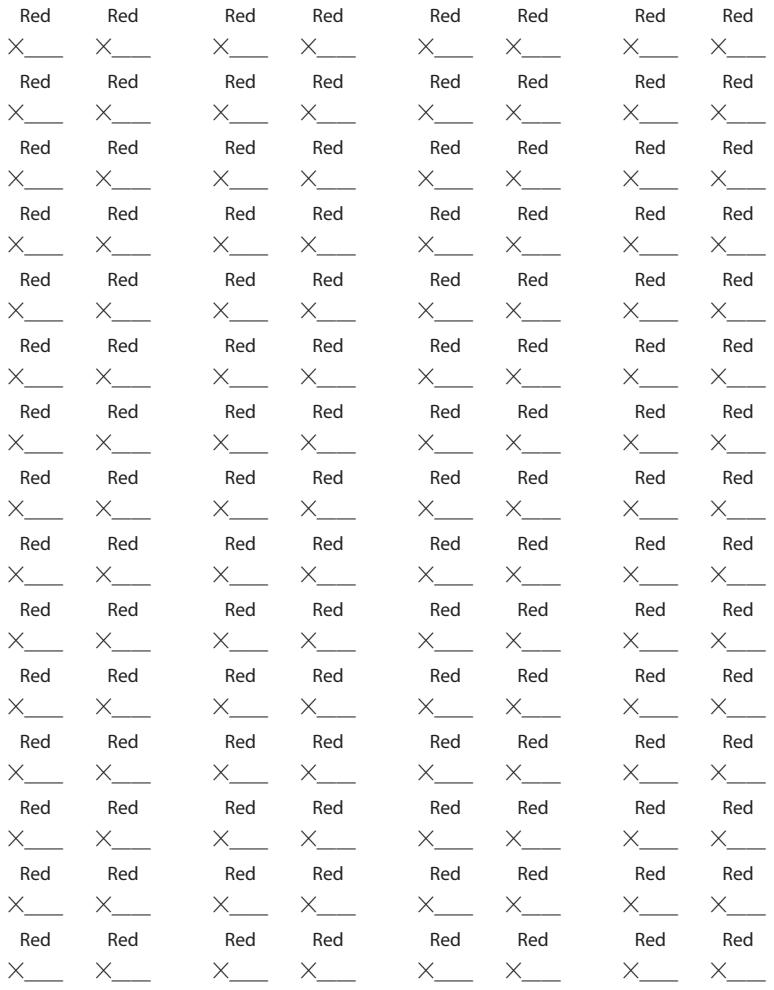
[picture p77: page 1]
Red ⨉____

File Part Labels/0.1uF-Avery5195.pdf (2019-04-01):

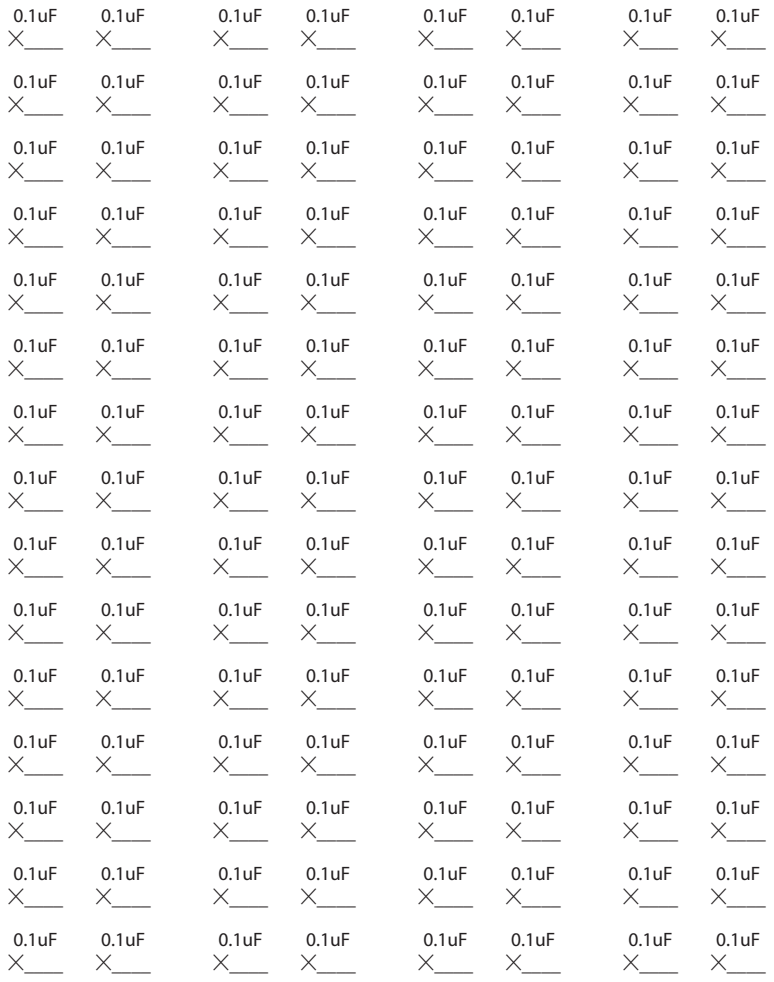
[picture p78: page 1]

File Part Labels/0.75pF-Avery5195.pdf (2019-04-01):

### ⨉____

### ⨉____

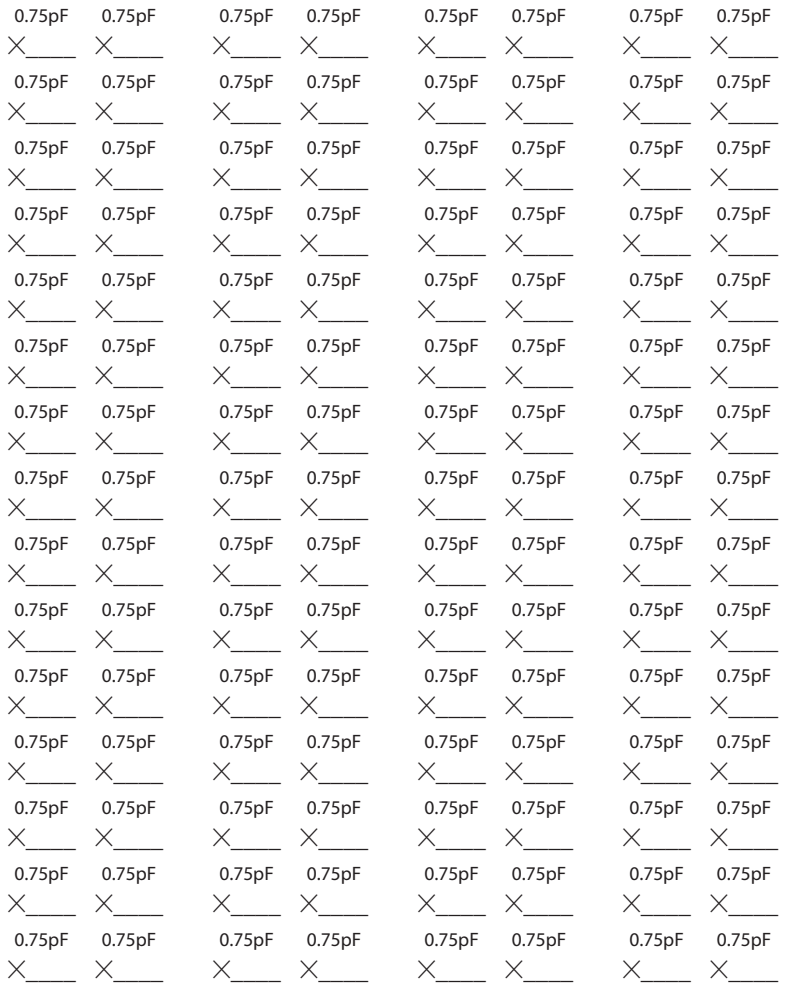
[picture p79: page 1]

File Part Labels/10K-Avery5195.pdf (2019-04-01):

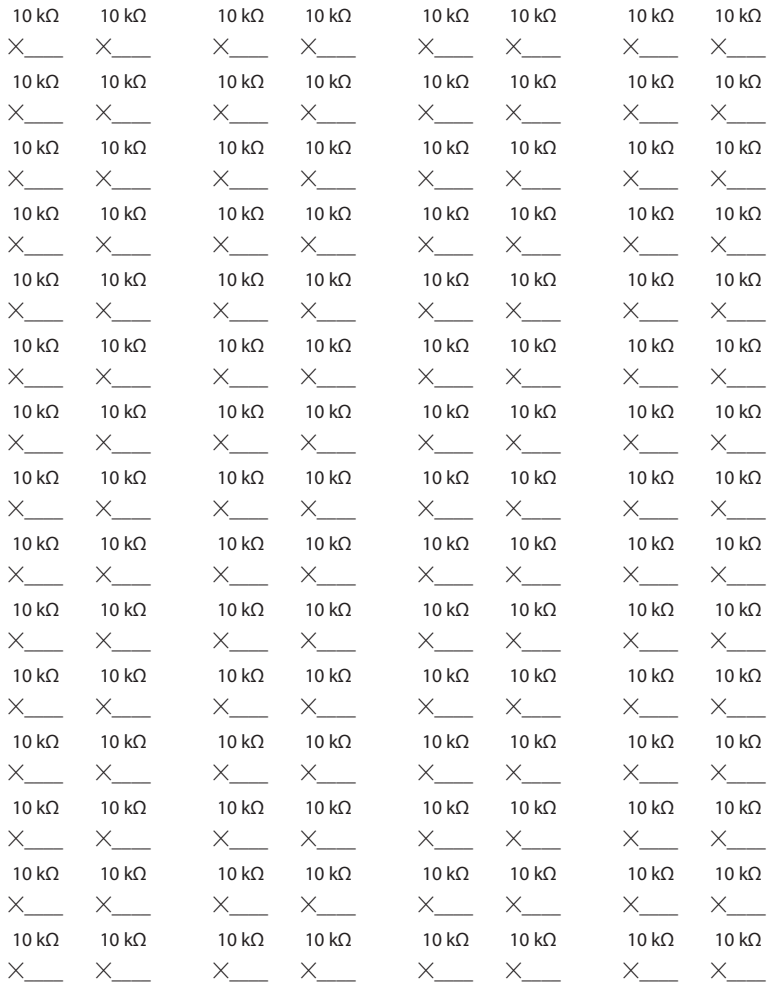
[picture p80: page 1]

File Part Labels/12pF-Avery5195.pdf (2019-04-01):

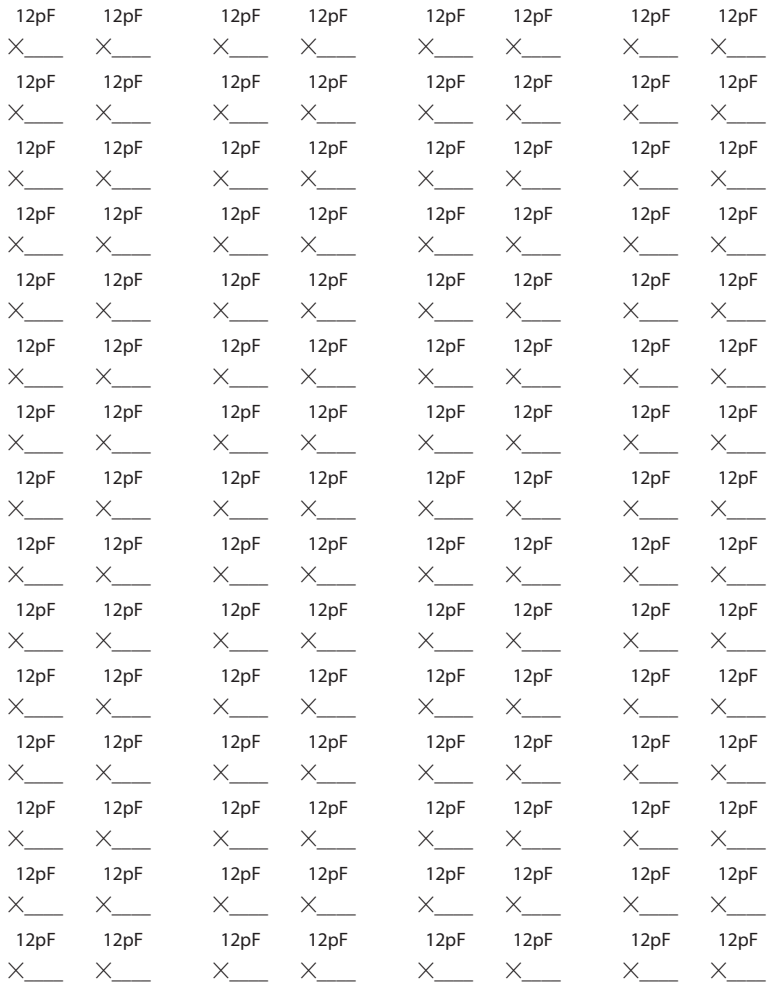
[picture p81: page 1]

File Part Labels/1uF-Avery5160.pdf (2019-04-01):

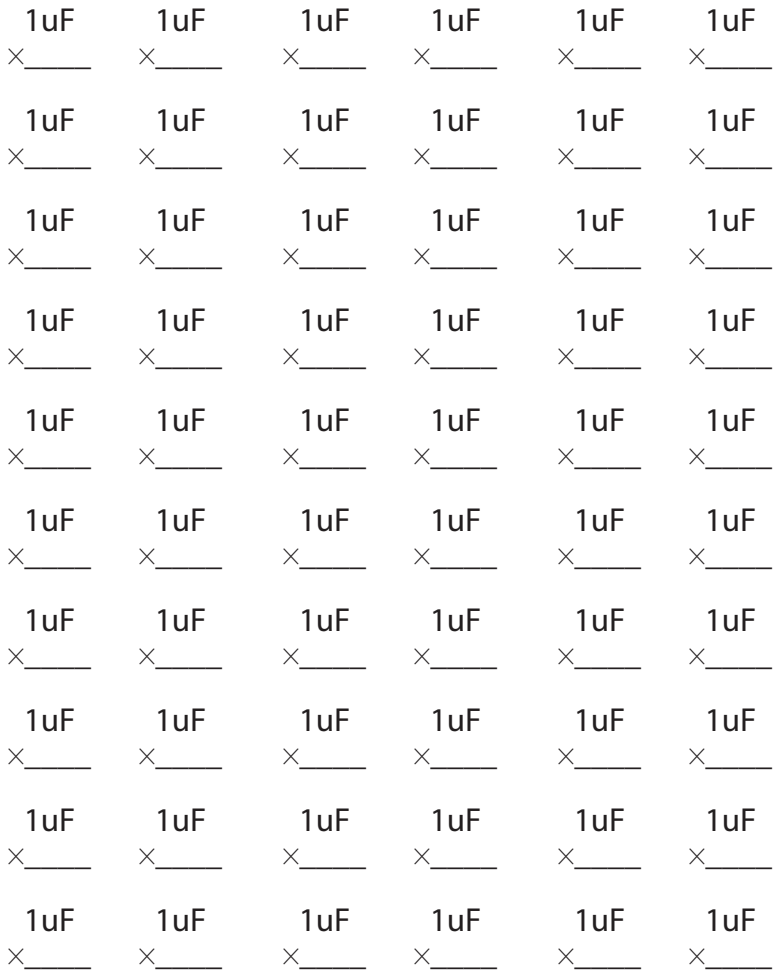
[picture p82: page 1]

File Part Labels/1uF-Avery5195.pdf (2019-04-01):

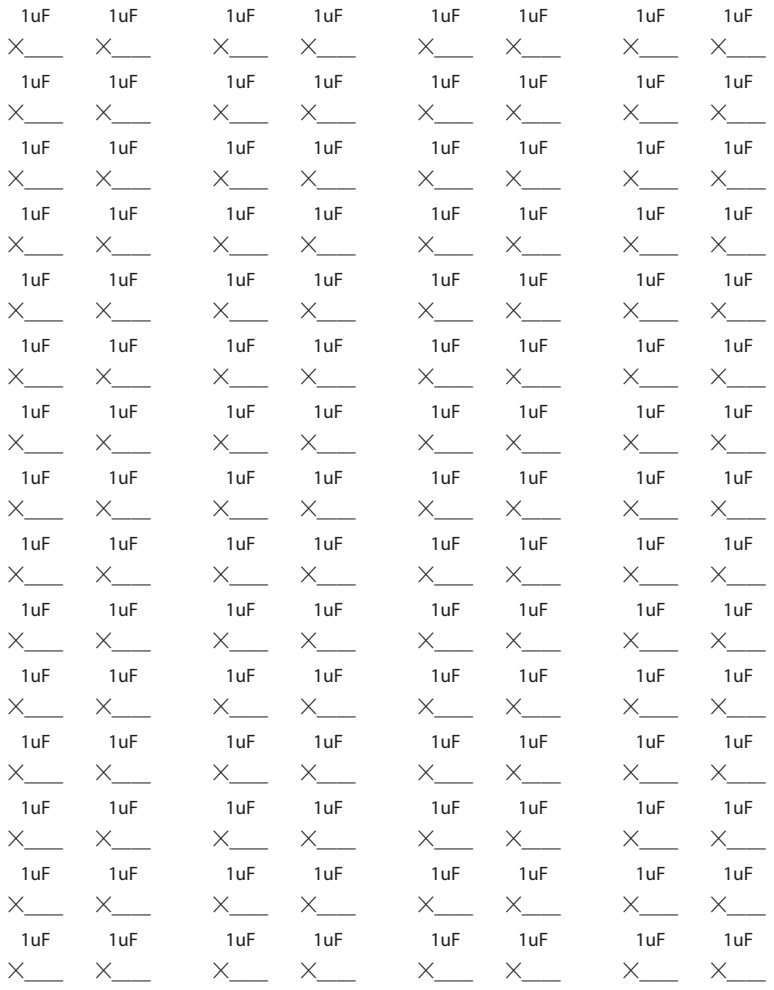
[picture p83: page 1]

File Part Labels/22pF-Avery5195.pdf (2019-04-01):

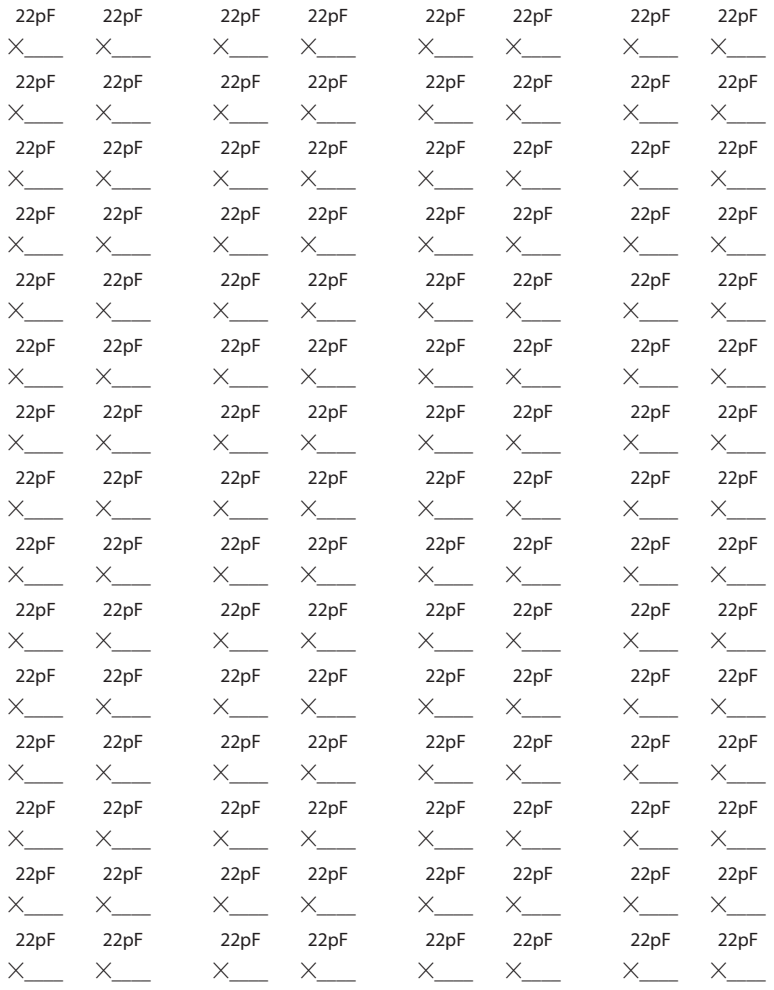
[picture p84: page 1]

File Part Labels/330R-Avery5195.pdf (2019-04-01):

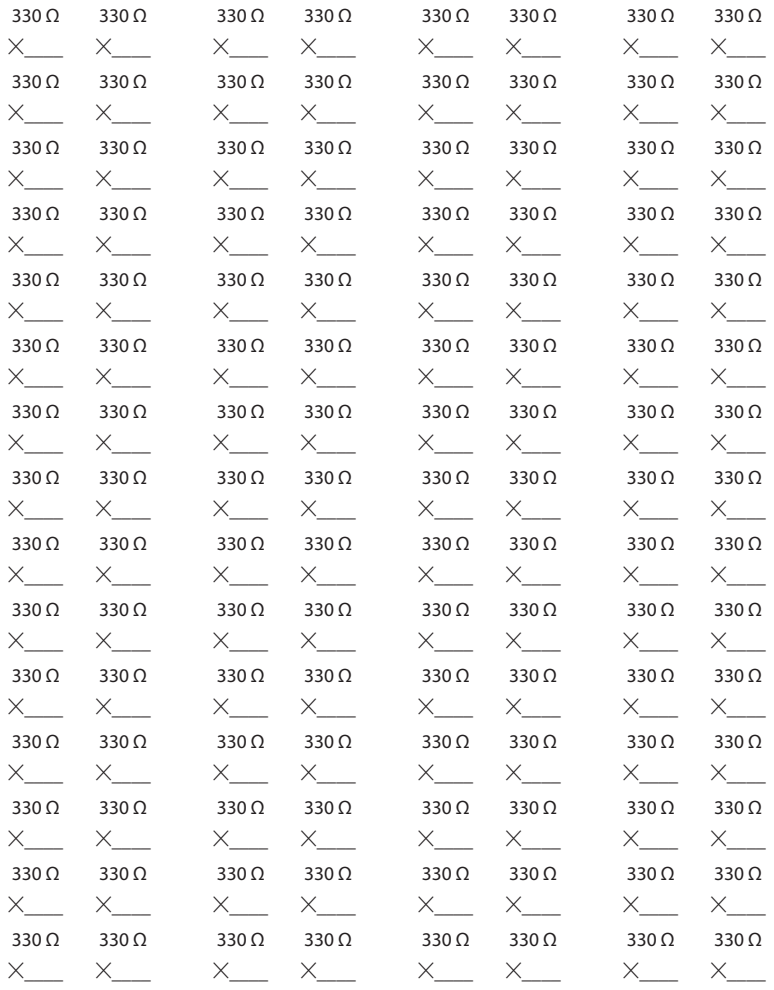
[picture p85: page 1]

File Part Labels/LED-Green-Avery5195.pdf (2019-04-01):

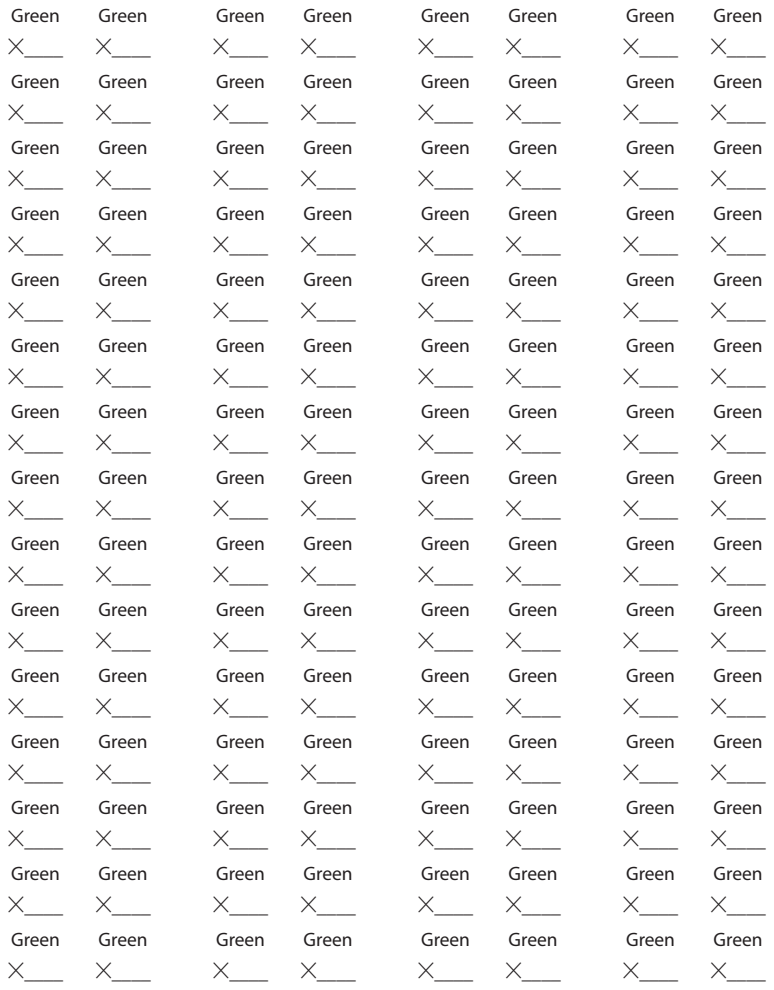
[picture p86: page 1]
Green ⨉____

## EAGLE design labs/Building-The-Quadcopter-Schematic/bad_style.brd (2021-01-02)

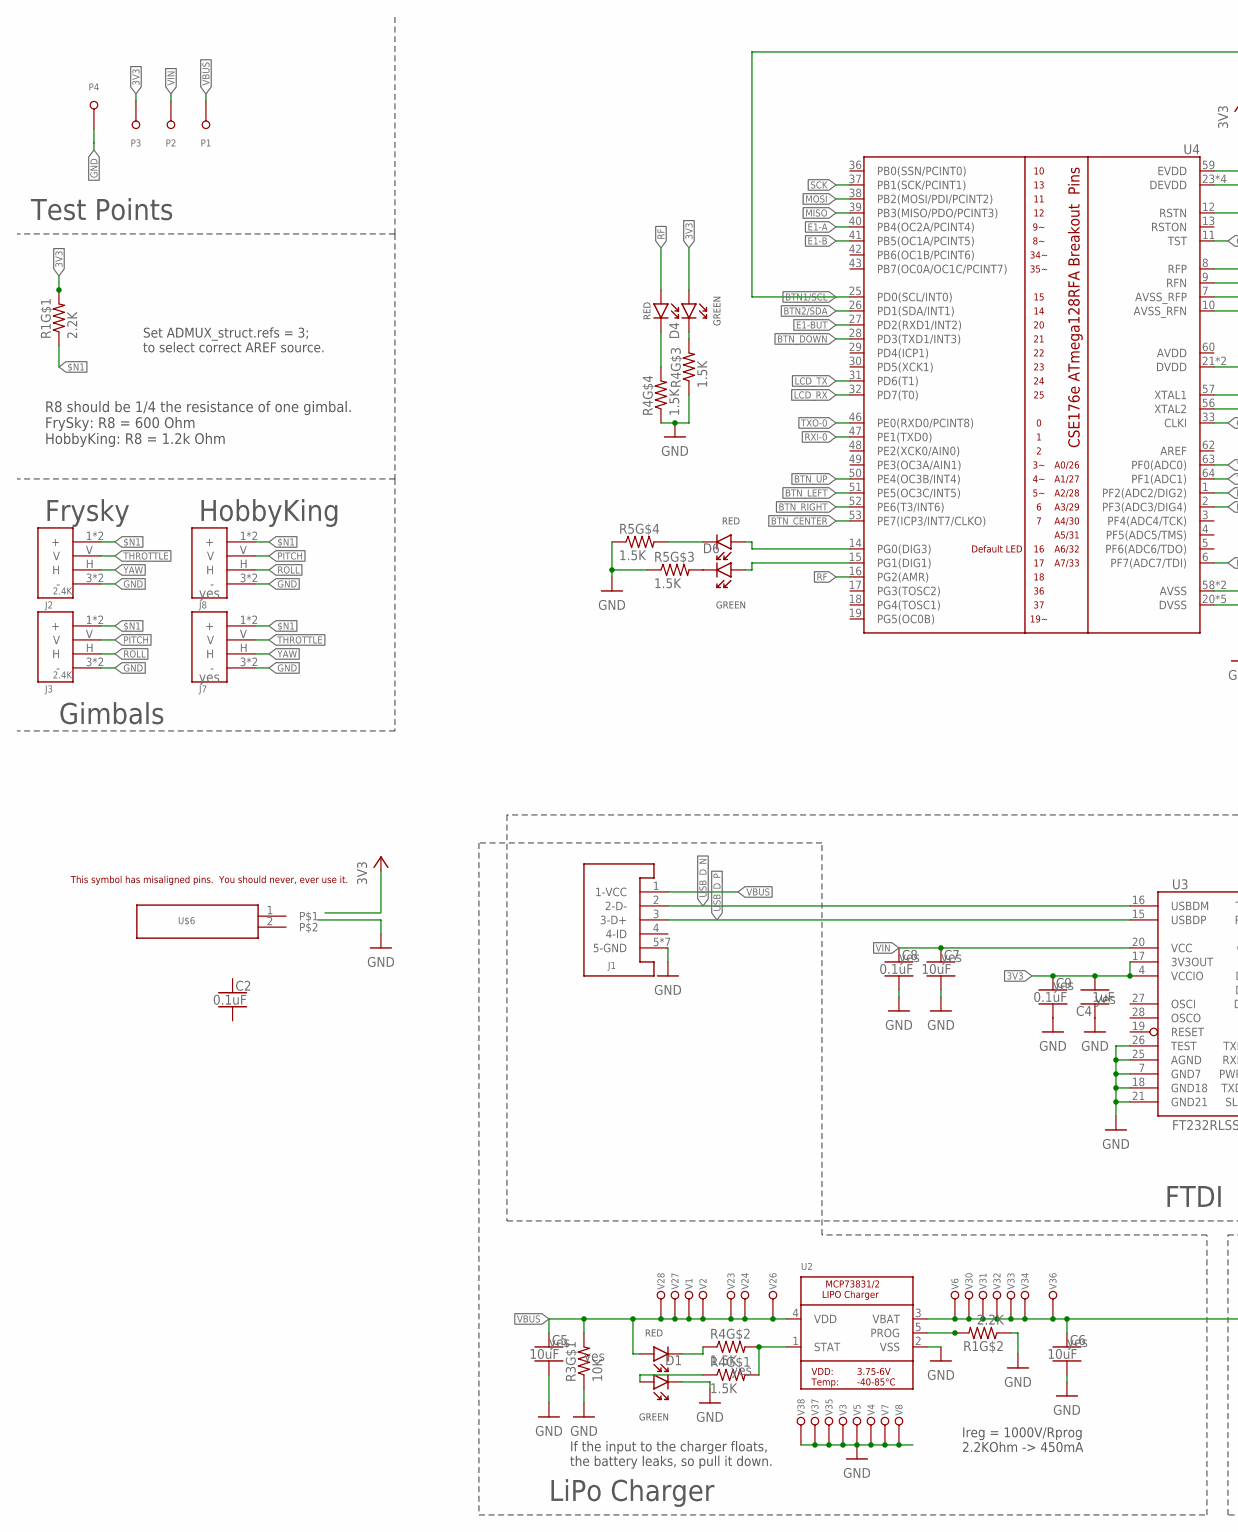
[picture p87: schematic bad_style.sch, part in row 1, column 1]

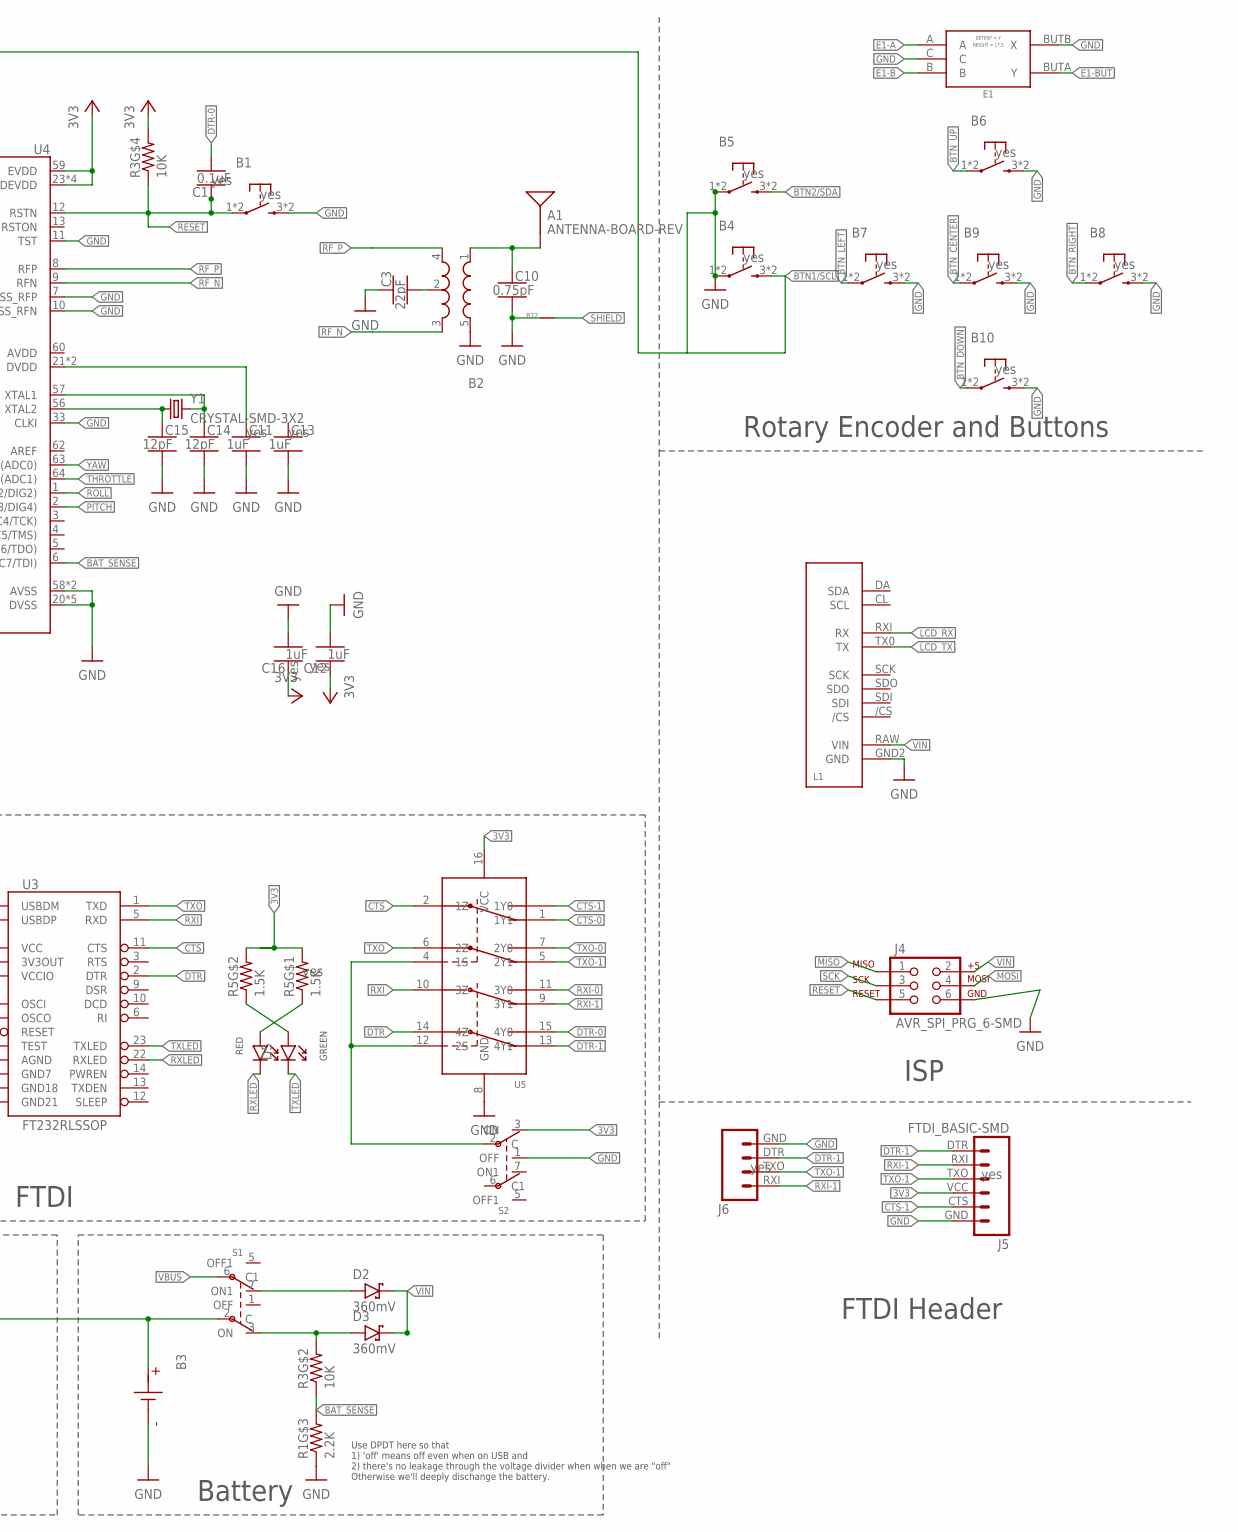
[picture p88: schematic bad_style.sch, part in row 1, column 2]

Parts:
A1: ANTENNA-BOARD-REV; ANT_PCB_2.4GHZ_NRF8001_1.6MM_1OZ_REV
B1, B4, B5, B6, B7, B8, B9, B10: PUSHBUTTON_-4.5X4.5; 4.5MM_TACTILE_SWITCH_TL3305AF160QG
B2: BALUN0805; BALUN
B3: BATTERY-SMD; MOLEX-BATTERY-CONNECTOR-SMD-51005-2P
B12: NET_BRIDGE
C1, C2, C8, C9: 0.1uF; CAPC1608X100
C3: 22pF; CAPC1608X100
C4, C11, C12, C13, C16: 1uF; CAPC1608X100
C5, C6, C7: 10uF; CAPC1608X100
C10: 0.75pF; CAPC1608X100
C14, C15: 12pF; CAPC1608X100
D1, D4, D5, D6: LED-2X-GREEN/RED-1.6X1.5MM; LED-2X-LITE-ON-1.6MMX1.5MM
D2, D3: 360mV; SODFL3516X96
E1: ROTARY-ENCODER-W/BUTTON-BOURNS-PEC12R-4217F; BOURNS-PEC12R
J1: USB-MICROA-AMPHENOL-10118192-0001LF; USB-MICROA-10118192-0001LF
J2, J3: 2.4K; JST-13-PTH
J4: AVR_SPI_PRG_6-SMD; 2X3-SMD
J5: FTDI_BASIC-SMD; FTDI-BASIC-SMD
J6: FTDI-4PIN-RIGHT-ANGLE-SMD; HEADER-2X2-0.1IN-MALE-RIGHT-ANGLE-SMD
J7, J8: FRSKY-GIMBAL-2X-SERVO-SMD; 2X-SERVO-SMD
L1: SPARKFUN_SERLCD_SERIAL_REDUCED-SMD; SPARKFUN_SERLCD_16X2_REDUCED_SMD
P1, P2, P3, P4: TEST-POINT; TEST-POINT-KEYSTONE-5000
R1: 2.2K; RESCAXS50P200X100X45-8
R3: 10K; RESCAXS50P200X100X45-8
R4, R5: 1.5K; RESCAXS50P200X100X45-8
S1, S2: SWITCH-DPDT-300MA-6V-SMD; JS202011JCQN
U2: MCP73831T-2ACI/OT; SOT23-5
U3: FT232RLSSOP; SSOP28DB
U4: ATMEGA128RFA1; QFN-64
U5: DPDT-X2; SOP65P640X110-16
U$6: DONT_USE; SCREW-TERMINAL-1X2-2.54MM
V1, V2, V3, V4, V5, V6, V7, V8, V23, V24, V26, V27, V28, V30, V31, V32, V33, V34, V35, V36, V37, V38: LOCKED-VIA-0.2; VIA-0.2MM
Y1: CRYSTAL-SMD-3X2; OSCCC320X250X85

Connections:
3V3: C4.2, C9.1, C12.1, C16.1, D4.A1, J5.VCC (4), P3.T, R1.5 (2), R3.8 (2), R5.5 (2), R5.6 (2), S2.3 (ON), U3.4 (VCCIO), U3.17 (3V3OUT), U4.23 (DEVDD), U4.34 (DEVDD), U4.44 (DEVDD), U4.54 (DEVDD), U4.59 (EVDD), U5.16 (VCC)
$N1: J2.1 (+), J2.4 (+), J3.1 (+), J3.4 (+), J7.1 (+), J7.4 (+), J8.1 (+), J8.4 (+), R1.4 (1)
ANTENNA: A1.FEED, B2.1 (IN), C10.1
BAT_SENSE: R1.7 (2), R3.3 (1), U4.6 (PF7(ADC7/TDI))
BCAP: B2.2 (GND), C3.2
BPOS: B3.P, C6.1, S1.2 (C), U2.3 (VBAT), V6.P1, V30.P1, V31.P1, V32.P1, V33.P1, V34.P1, V36.P1
BTN1/SCL: B4.3 (2), B4.4 (2), U4.25 (PD0(SCL/INT0))
BTN2/SDA: B5.3 (2), B5.4 (2), U4.26 (PD1(SDA/INT1))
BTN_CENTER: B9.1, B9.2 (1), U4.53 (PE7(ICP3/INT7/CLKO))
BTN_DOWN: B10.1, B10.2 (1), U4.28 (PD3(TXD1/INT3))
BTN_LEFT: B7.1, B7.2 (1), U4.51 (PE5(OC3C/INT5))
BTN_RIGHT: B8.1, B8.2 (1), U4.52 (PE6(T3/INT6))
BTN_UP: B6.1, B6.2 (1), U4.50 (PE4(OC3B/INT4))
CLK_NEG: C15.1, U4.56 (XTAL2), Y1.1
CLK_POS: C14.1, U4.57 (XTAL1), Y1.3 (2)
CTS: U3.11 (CTS), U5.2 (1Z)
CTS-0: U5.3 (1Y0)
CTS-1: J5.CTS (5), U5.1 (1Y1)
DTR: U3.2 (DTR), U5.14 (4Z)
DTR-0: C1.2, U5.15 (4Y0)
DTR-1: J5.DTR (1), J6.DTR (3), U5.13 (4Y1)
E1-A: E1.A, U4.40 (PB4(OC2A/PCINT4))
E1-B: E1.B, U4.41 (PB5(OC1A/PCINT5))
E1-BUT: E1.BUTA (Y), U4.27 (PD2(RXD1/INT2))
GND: B1.3 (2), B1.4 (2), B2.5 (GND), B3.G (N), B3.G2 (N), B3.G3 (N), B4.1, B4.2 (1), B5.1, B5.2 (1), B6.3 (2), B6.4 (2), B7.3 (2), B7.4 (2), B8.3 (2), B8.4 (2), B9.3 (2), B9.4 (2), B10.3 (2), B10.4 (2), B12.P1, C3.1, C4.1, C5.2, C6.2, C7.2, C8.2, C9.2, C10.2, C11.2, C12.2, C13.2, C14.2, C15.2, C16.2, D1.C1, E1.BUTB (X), E1.C, J1.5 (5-GND), J1.6 (5-GND), J1.7 (5-GND), J1.8 (5-GND), J1.9 (5-GND), J1.10 (5-GND), J1.11 (5-GND), J2.3 (-), J2.6 (-), J3.3 (-), J3.6 (-), J4.6, J5.GND (6), J6.GND (4), J7.3 (-), J7.6 (-), J8.3 (-), J8.6 (-), L1.GND2 (GND), P4.T, R1.2 (1), R1.3 (1), R3.4 (1), R4.1, R4.2 (1), R5.1, R5.2 (1), S2.1 (OFF), U2.2 (VSS), U3.7 (GND7), U3.18 (GND18), U3.21 (GND21), U3.25 (AGND), U3.26 (TEST), U4.7 (AVSS_RFP), U4.10 (AVSS_RFN), U4.11 (TST), U4.20 (DVSS), U4.24 (DVSS), U4.33 (CLKI), U4.35 (DVSS), U4.45 (DVSS), U4.55 (DVSS), U4.58 (AVSS), U4.61 (AVSS), U5.8 (GND), V3.P1, V4.P1, V5.P1, V7.P1, V8.P1, V35.P1, V37.P1, V38.P1
LCD_RX: L1.RXI (RX), U4.32 (PD7(T0))
LCD_TX: L1.TX0 (TX), U4.31 (PD6(T1))
MISO: J4.1, U4.39 (PB3(MISO/PDO/PCINT3))
MOSI: J4.4, U4.38 (PB2(MOSI/PDI/PCINT2))
unnamed: D1.A1, R4.4 (1)
unnamed: D1.C2, R4.3 (1)
unnamed: D5.A1, R5.3 (1)
unnamed: D6.C2, R5.8 (2)
unnamed: D6.C1, R5.7 (2)
unnamed: D4.C1, R4.7 (2)
unnamed: D5.A2, R5.4 (1)
unnamed: D6.A2, U4.14 (PG0(DIG3))
unnamed: D6.A1, U4.15 (PG1(DIG1))
unnamed: R4.5 (2), R4.6 (2), U2.1 (STAT)
unnamed: R1.6 (2), U2.5 (PROG)
unnamed: D4.C2, R4.8 (2)
unnamed: D2.2 (A), S1.7 (ON1)
unnamed: C11.1, U4.21 (DVDD), U4.22 (DVDD)
PITCH: J3.V, J8.V, U4.2 (PF3(ADC3/DIG4))
PROG_SEL: S2.2 (C), U5.4 (1S), U5.12 (2S)
RESET: B1.1, B1.2 (1), C1.1, J4.5, R3.1, U4.12 (RSTN)
RF: D4.A2, U4.16 (PG2(AMR))
RF_N: B2.3 (OUT2), U4.9 (RFN)
RF_P: B2.4 (OUT1), U4.8 (RFP)
ROLL: J3.H, J8.H, U4.1 (PF2(ADC2/DIG2))
RXI: U3.5 (RXD), U5.10 (3Z)
RXI-0: U4.47 (PE1(TXD0)), U5.11 (3Y0)
RXI-1: J5.RXI (2), J6.RXI (1), U5.9 (3Y1)
RXLED: D5.C2, U3.22 (RXLED)
SCK: J4.3, U4.37 (PB1(SCK/PCINT1))
SHIELD: B12.P2
THROTTLE: J2.V, J7.V, U4.64 (PF1(ADC1))
TXLED: D5.C1, U3.23 (TXLED)
TXO: U3.1 (TXD), U5.6 (2Z)
TXO-0: U4.46 (PE0(RXD0/PCINT8)), U5.7 (2Y0)
TXO-1: J5.TXO (3), J6.TXO (2), U5.5 (2Y1)
USB_D_N: J1.2 (2-D-), U3.16 (USBDM)
USB_D_P: J1.3 (3-D+), U3.15 (USBDP)
VBAT: D3.2 (A), R3.6 (2), S1.3 (ON)
VBUS: C5.1, D1.A2, J1.1 (1-VCC), P1.T, R3.5 (2), S1.6 (C1), U2.4 (VDD), V1.P1, V2.P1, V23.P1, V24.P1, V26.P1, V27.P1, V28.P1
VIN: C7.1, C8.1, D2.1 (C), D3.1 (C), J4.2, L1.RAW (VIN), P2.T, U3.20 (VCC)
YAW: J2.H, J7.H, U4.63 (PF0(ADC0))

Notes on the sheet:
Ireg = 1000V/Rprog 2.2KOhm -> 450mA
LiPo Charger
Test Points
Frysky
HobbyKing
Rotary Encoder and Buttons
Battery
ISP
FTDI Header
Set ADMUX_struct.refs = 3; to select correct AREF source.
Gimbals
R8 should be 1/4 the resistance of one gimbal. FrySky: R8 = 600 Ohm HobbyKing: R8 = 1.2k Ohm
If the input to the charger floats, the battery leaks, so pull it down.
FTDI
Use DPDT here so that 1) 'off' means off even when on USB and 2) there's no leakage through the voltage divider when when we are "off" Otherwise we'll deeply dischange the battery.

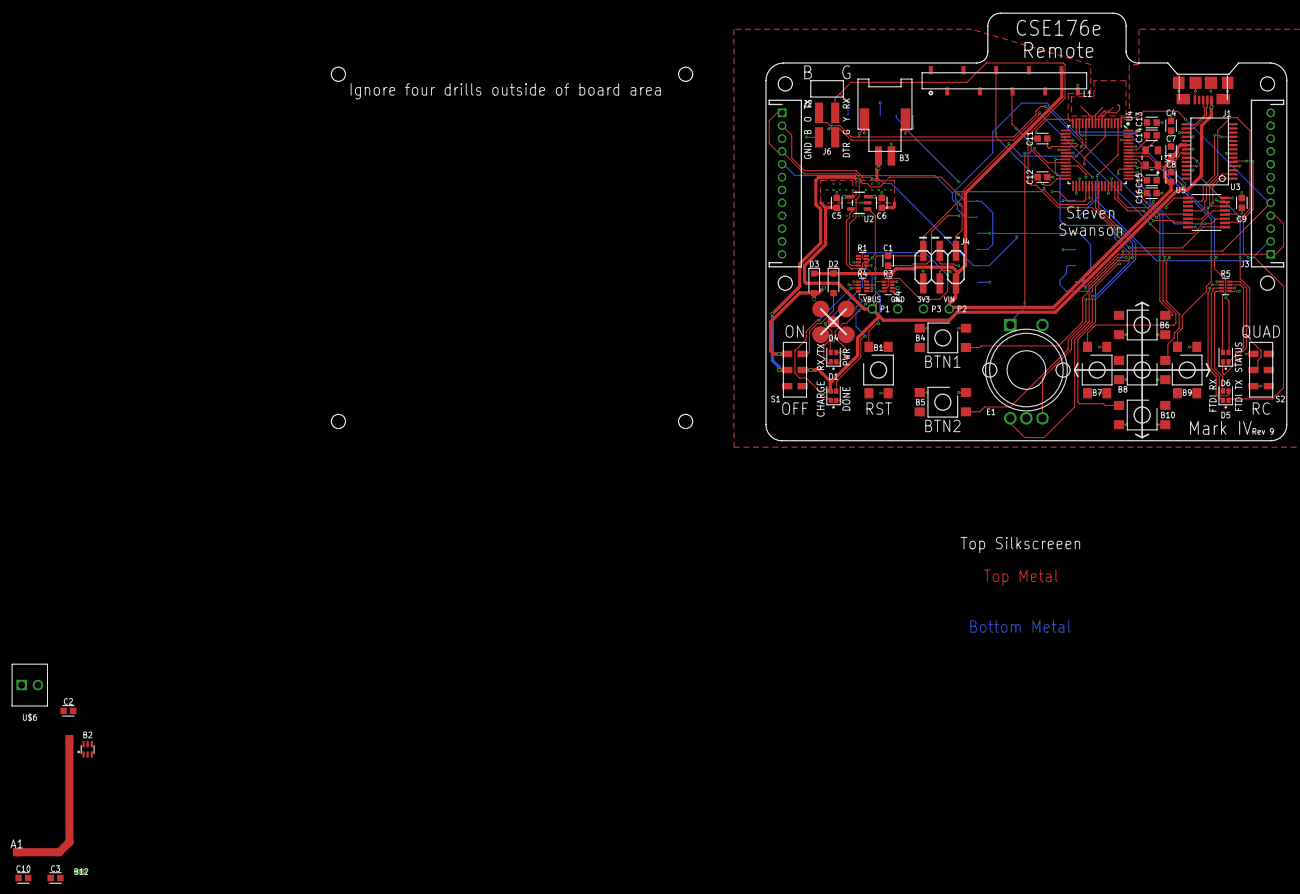
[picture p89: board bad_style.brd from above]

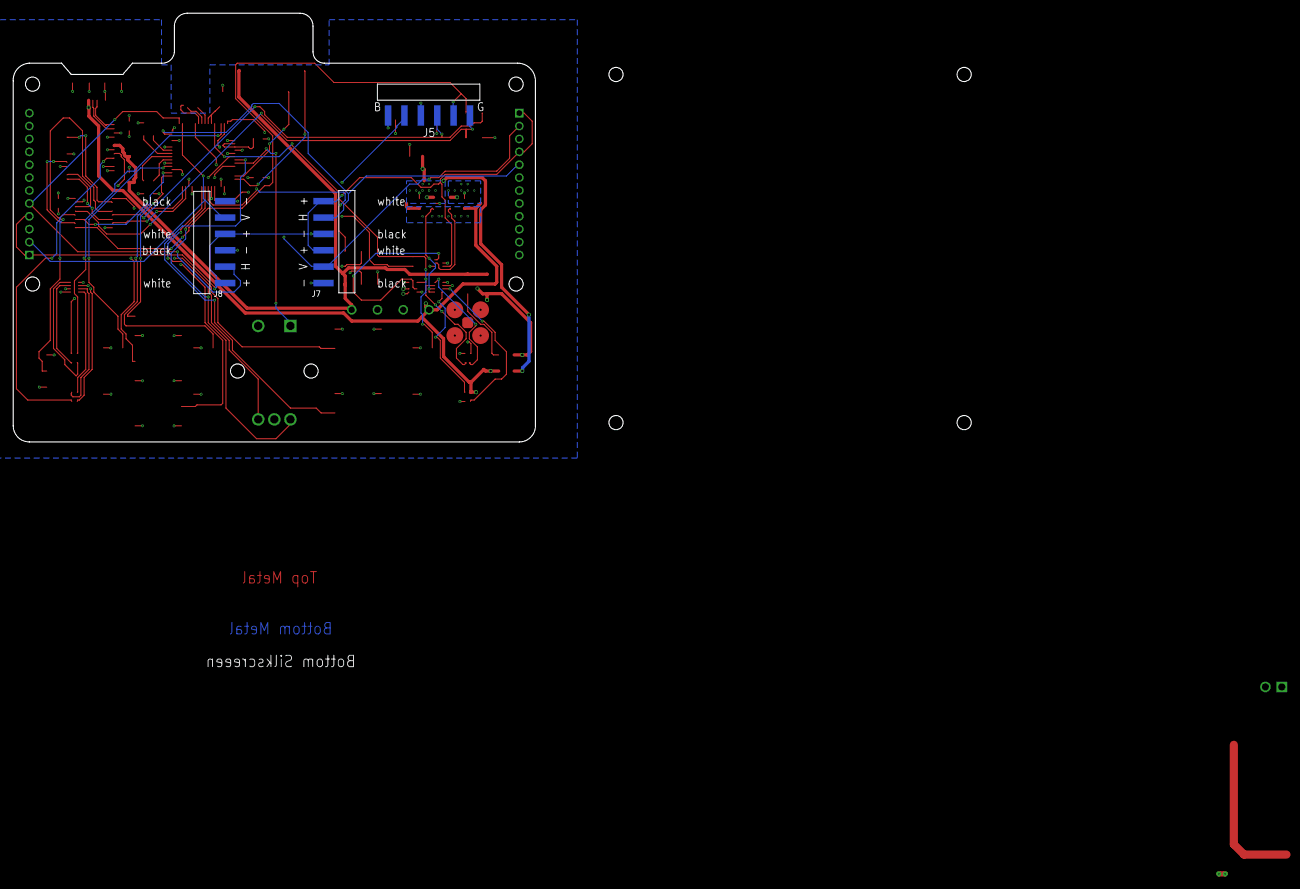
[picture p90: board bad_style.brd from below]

Board: 4 copper layers, 81.0 x 66.5 mm, 89 parts (3 on the bottom side), 65 nets.

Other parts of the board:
E$1, E$2: FRSKY-TARANIS-GIMBAL
U$1: 700MAH-BATTERY
U$2: QUADCLASS_LOGO_SMALL
U$3: LAYER_LABELS
U$4: 375MAH-BATTERY
U$5: 600MAH-BATTERY

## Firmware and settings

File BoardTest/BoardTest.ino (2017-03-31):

/*
  ATmega128RFA1 Dev Board Basic Test
  by: Jim Lindblom
      SparkFun Electronics
  date: July 3, 2012
  License: Beerware. Feel free to use, reuse, and modify this code
  as you please. If you find it useful, you can buy me a beer.

  This code sets up the ATmega128RFA1's wireless transciever in
  the most basic way possible to serve as a serial gateway.
  Serial into the ATmega128RFA1's UART0 will go out the RF radio.
  Data into the RF radio will go out the MCU's UART0.

  Modify to test other functionality.....?
  
*/

#include "BoardFunctions.h"

void setup()
{
  Serial.begin(9600);  // Start up serial
  Serial1.begin(115200);
  rfBegin(11);  // Initialize ATmega128RFA1 radio on channel 11 (can be 11-26)
  
  // Send a message to other RF boards on this channel
  rfPrint("ATmega128RFA1 Dev Board Online!\r\n");
}

void loop()
{
  
  if (Serial.available())  // If serial comes in...
  {
    rfWrite(Serial.read()); // ...send it out the radio.
  }
  if (rfAvailable())  // If data receievd on radio...
  {
    Serial.print(rfRead());  // ... send it out serial.
  }
}

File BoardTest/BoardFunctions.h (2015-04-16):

/* RadioFunctions.h
  A handful of sending and receiving functions for the 
  ATmega128RFA1.
  by: Jim Lindblom
      SparkFun Electronics
  date: July 8, 2013
  license: Beerware. Use, distribut, and modify this code freely
  however you please. If you find it useful, you can buy me a beer
  some day.
  
  Functions in here:
    rfBegin(uint8_t channel) - Initializes the radio on a channel
                                between 11 and 26.
    rfWrite(uint8_t b) - Sends a byte over the radio.
    rfPrint(String toPrint) - Sends a string over the radio.
    int rfAvailable() - Returns number of characters currently
                        in receive buffer, ready to be read.
    char rfRead() - Reads a character out of the buffer.
    
  Interrupt Sub-Routines (ISRs) in here:
    TRX24_TX_END_vect - End of radio transfer.
    TRX24_RX_START_vect - Beginning of radio receive.
    TRX24_RX_END_vect - End of radio receive. Characters are 
                        collected into a buffer here.
*/
  
#include <Arduino.h> // Required for digitalWrites, etc.

// Board pin definitions.
const int RX_LED = 34;  // B6 - RF RX LED
const int TX_LED = 35;  // B7 - RF TX LED
uint8_t rssiRaw; // Global variable shared between RX ISRs

// A buffer to maintain data being received by radio.
const int RF_BUFFER_SIZE = 127;
struct ringBuffer
{
  unsigned char buffer[RF_BUFFER_SIZE];
  volatile unsigned int head;
  volatile unsigned int tail;
} radioRXBuffer;


// Initialize the RFA1's low-power 2.4GHz transciever.
// Sets up the state machine, and gets the radio into
// the RX_ON state. Interrupts are enabled for RX
// begin and end, as well as TX end.
uint8_t rfBegin(uint8_t channel)
{
  for (int i=0; i<128; i++)
  {
    radioRXBuffer.buffer[i] = 0;
  }
  radioRXBuffer.tail = 0;
  radioRXBuffer.head = 0;

  // Setup RX/TX LEDs: These are pins B6/34 (RX) and B7/35 (TX).
  pinMode(RX_LED, OUTPUT);
  digitalWrite(RX_LED, LOW);
  pinMode(TX_LED, OUTPUT);
  digitalWrite(TX_LED, LOW);

  // Transceiver Pin Register -- TRXPR.
  // This register can be used to reset the transceiver, without
  // resetting the MCU.
  TRXPR |= (1<<TRXRST);   // TRXRST = 1 (Reset state, resets all registers)

  // Transceiver Interrupt Enable Mask - IRQ_MASK
  // This register disables/enables individual radio interrupts.
  // First, we'll disable IRQ and clear any pending IRQ's
  IRQ_MASK = 0;  // Disable all IRQs
  
  // Transceiver State Control Register -- TRX_STATE
  // This regiseter controls the states of the radio.
  // First, we'll set it to the TRX_OFF state.
  TRX_STATE = (TRX_STATE & 0xE0) | TRX_OFF;  // Set to TRX_OFF state
  delay(1);
  
  // Transceiver Status Register -- TRX_STATUS
  // This read-only register contains the present state of the radio transceiver.
  // After telling it to go to the TRX_OFF state, we'll make sure it's actually
  // there.
  if ((TRX_STATUS & 0x1F) != TRX_OFF) // Check to make sure state is correct
    return 0;	// Error, TRX isn't off

  // Transceiver Control Register 1 - TRX_CTRL_1
  // We'll use this register to turn on automatic CRC calculations.
  TRX_CTRL_1 |= (1<<TX_AUTO_CRC_ON);  // Enable automatic CRC calc. 
  
  // Enable RX start/end and TX end interrupts
  IRQ_MASK = (1<<RX_START_EN) | (1<<RX_END_EN) | (1<<TX_END_EN);
  
  // Transceiver Clear Channel Assessment (CCA) -- PHY_CC_CCA
  // This register is used to set the channel. CCA_MODE should default
  // to Energy Above Threshold Mode.
  // Channel should be between 11 and 26 (2405 MHz to 2480 MHz)
  if ((channel < 11) || (channel > 26)) channel = 11;  
  PHY_CC_CCA = (PHY_CC_CCA & 0xE0) | 11; // Set the channel to 11
  
  // Finally, we'll enter into the RX_ON state. Now waiting for radio RX's, unless
  // we go into a transmitting state.
  TRX_STATE = (TRX_STATE & 0xE0) | RX_ON; // Default to receiver

  return 1;
}
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

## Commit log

2013-01-22 Hardware initial commit (v22 design)
    [ATmega128RFA1-DevBoard.brd, ATmega128RFA1-DevBoard.sch]
2013-05-06 Minor silkscreen fixes - v23
    [ATmega128RFA1-DevBoard.brd, ATmega128RFA1-DevBoard.sch]
2013-05-07 More minor silkscreen fixes
    [ATmega128RFA1-DevBoard.brd, ATmega128RFA1-DevBoard.sch]
2013-05-07 v23 Production Ready
    Added fiducials to design files
    Created production panel of 4 boards
    [ATmega128RFA1-DevBoard-Panel-v23.brd]
2013-06-28 Initial bootloader, test sketch, boards.txt commit
    Adding everything in the firmware folder:
    * fimrware/Arduino/hardware - Arduino addon for the ATmega128RFA1 dev
    board. Also includes install for updated version of WinAVR. Check out
    the readme for installation instructions.
    * firmware/Sketches - Example test sketches for a simple RF ping between
    two ATmega128RFA1 dev boards. This is currently the code used in
    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
2013-07-02 Adding/re-ordering pin definitions
    This should make all pins on the dev board addressable via pin numbers.
    digitalWrite, digitalRead, analogWrite, and analogRead should all on the
    pin numbers. Wire and SPI libraries have also been tested for
    functionality.
2015-03-11 Updating boards.txt, adding platform.txt, removing cores folder.
2015-03-11 Re-organizing directory structure to meet Arduino specifications.
2015-03-11 Revising readme.md to match current installation directions.
2015-03-29 Adding BlinkTest and BasicChat Code
    BlinkTest
    This is a small code to test you can upload code to the ATmega128RFA1
    Dev Board.
    BasicChat
    BasicChat code from sparkfun with bug fixed.
2015-04-02 update slides
    [Myduino.brd, Myduino.koala.sch, Myduino.sch]
2015-04-06 Adding Gimbals and Motor Driver schematics for Lab3
2015-04-06 Adding Motor Board Schematic
    [Motor_board_Rev0.brd, Motor_board_Rev0.sch]
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2015-04-07 latest updates
    [Motor_board_Rev0.brd]
2015-04-08 lab 4 stuff
    [controller_board.brd, controller_board.sch]
2015-04-08 fixed layers in controller board
    [controller_board.brd, controller_board.sch]
2015-04-09 Adding Datasheets for Lab4
    [controller_board.brd, controller_board.sch]
2015-04-09 final tweaks
    [controller_board.brd]
2015-04-09 Adding SMD Mosfet and Diode Datasheets
2015-04-16 Added missing datasheets and devices for Lab5
2015-04-19 Controller board with correct drill sizes.
    [controller_board.brd, controller_board.sch]
2015-04-20 MotorDriver.pdf recommended pins changes
2015-04-23 fixed pin on power supply
2015-04-27 LSM9DS0 Breakout Board
    Breakout Board of the LSM9DS0
    [LSM9DS0_Breakout_Board-panel2.brd, LSM9DS0_Breakout_Board.brd, LSM9DS0_Breakout_Board.sch]
2015-04-28 LSM9DS0 Breakout Board fix
    [LSM9DS0_Breakout_Board-panel3.brd, LSM9DS0_Breakout_Board-panel4.brd, LSM9DS0_Breakout_Board.brd]
2015-04-28 LSM9DS0 Breakout Board fix 2
    [LSM9DS0_Breakout_Board-panel5.brd]
2015-04-30 Added Green LED datasheet.
2015-05-05 Adding MultiWii Software to Lab8
    [config.h]
2015-05-19 Controller schematic
    [LSM9DS0_Breakout_Board.csv, controller_connect_board.brd, controller_connect_board.sch]
2015-05-20 Controller Tests for Button, Gimbals and LCD
2015-05-22 IMU Test For the breakout board and the Quadcopter
2015-06-02 Adding Multiwii Experimental
    [config.h]
2015-06-02 Adding My Schematic for the Quadcopter
    [UCSD_QuadCopter_Rev1.brd, UCSD_QuadCopter_Rev1.sch]
2015-06-04 MultiWii Test, Code with No Internal PullUps
    [config.h]
2015-06-09 Firmware for the Controller Gimbals that are Switched
2015-06-17 Quadcopter and Controller BOM
    [CSE190F_BOM.xlsx]
2016-03-30 Adding hardware file that fixes uploading problems for Arduino versions 1.6.6, 1.6.7 and 1.6.8 ...
2016-03-31 updated slides
    [ATmega128RFA1-DevBoard.brd, ATmega128RFA1-DevBoard.sch]
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2016-05-17 Adding the 3D models of the stands
    [STAND_ALONE_RV1.stl, STAND_WITH_PARTS_RV1.stl]
2017-03-25 clean up
    [ATmega128RFA1-DevBoard-Panel-v23.brd, ATmega128RFA1-DevBoard.brd, ATmega128RFA1-DevBoard.sch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]
2017-04-03 examples for board layout/placement
    [ATmega128RFA1-DevBoard.brd, ATmega128RFA1-DevBoard.sch, Myduino-placed.brd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]
2017-04-03 gitignore. update examples
    [Myduino-placed.brd, Myduino-placed.sch]
2017-04-20 new slides
    [Myduino-placed.brd, Myduino.brd, Myduino.sch]
2018-04-05 Updates for 2018
    [ATmega128RFA1-DevBoard-unplaced.brd, ATmega128RFA1-DevBoard-unplaced.sch]
2018-05-05 add new DRU with 5mil traces
2018-05-25 tweak solder mask settings
2018-08-23 Use correct gerber output. Correct 2 layer setup
2018-08-23 Reduced stencil hole DRUs
2019-01-08 remove board outline from stencil
2019-02-08 moved quadparts_prebuilt.lbr to this repo
    [empty.brd, empty.sch]
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2019-02-20 new slides, new todos, update lib. A bunch of new lab write ups
    [empty.brd, empty.sch]
2019-02-22 remove the design review from the schematic lab
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2019-02-25 lots of work on the labs
    [remote+pwr+ftdi+gim+lcd+IMU+tp.digikey-bom.csv, remote+pwr+ftdi+gim+lcd+IMU.digikey-bom.csv, remote+pwr+ftdi+gim+lcd.digikey-bom.csv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]
2019-03-03 A bunch of changes:
    1. Add layer labels and quad logo to prebuilt library
    2. Add layer labels and quad logo to prebuilt library and errors
    3. massive lab and slide reorg
    4. new images
    5. New make file
    6. new slides
    [ATmega128RFA1-DevBoard-unplaced.brd, ATmega128RFA1-DevBoard-unplaced.sch, ATmega128RFA1-DevBoard.brd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]
2019-03-15 use screws instead of zip ties for the FCB/Airframe
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2019-04-10 Clarify parts of the IMU part spec. New DRC rules for solder mask
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2019-04-21 Get rid of VIN and the associated diode. Connect 3v3 to FTDI. Don't connect ISP to 3v3.
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2019-05-03 update IMU pad guidance to account for trace spacing
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2019-05-09 update about building your own remote
    [remote+pwr+ftdi+gim+lcd+IMU+tp.digikey-bom.csv, remote+pwr+ftdi+gim+lcd+IMU.digikey-bom.csv, remote+pwr+ftdi+gim+lcd.digikey-bom.csv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]
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2019-05-18 include bom in release. Order 5 sets of parts by default
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2021-01-02 bad schematic example
    [bad_style.brd, bad_style.sch]
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2021-01-12 add note about polarity in the LED package.
2021-01-12 add some notes about the IMU schematic symbol.
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2021-02-04 ADd guidance about having your pours cut in half. Update guidance about pour widths.
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2021-03-04 Added note about the radio blinking an led.
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2022-01-20 use correct battery device.
2022-02-05 slides updates an restore missing page of IMU datasheet
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2022-03-08 Fixed Table in Assembling PCB
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2023-04-12 Fix IMU git
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2023-04-17 Add missing constants link for IMU
2023-04-18 fix battery component.
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2023-09-13 Slides as of the end of Spring 2023
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2024-10-17 Update README.md
    fix gyro filter instructions.
2024-10-29 Change board layout trace width based on new Fusion360 version
